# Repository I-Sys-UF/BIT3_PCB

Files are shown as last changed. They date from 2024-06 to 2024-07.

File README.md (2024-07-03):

# BIT3_PCB

KiCad 7.0.x にて設計

# BIT とは

**B**eginning **I**.Sys **T**racer のイニシャルで、新入生教育用のライントレーサの筐体です  
先代の BIT2 の設計を踏襲しつつ、マイコンを RP2040 搭載の秋月製 AE-RP2040 に置き換えました。ギアボックス等は流用できるようにしています

# 部品表

## 主要部品

| 部品番号 | 部品名 | 秋月 |
|:----|:----|:----|
| R1 - R5, R11 | 100 Ω | [125101](https://akizukidenshi.com/catalog/g/g125101/) |
| R6 - R10 | 4.7k Ω | [125273](https://akizukidenshi.com/catalog/g/g125273/) |
| R12 - R16 | 510 Ω | [125511](https://akizukidenshi.com/catalog/g/g125511/) |
| R17 - R21 | 1k Ω | [125102](https://akizukidenshi.com/catalog/g/g125102/) |
| C1 - C3 | 0.1 uF | [110147](https://akizukidenshi.com/catalog/g/g110147/) |
| D1 - D5 | 5mm LED | [113172](https://akizukidenshi.com/catalog/g/g113172/) |
| D6 | 1N4148 | [100941](https://akizukidenshi.com/catalog/g/g100941/) |
| U1 | AE-RP2040 | [117542](https://akizukidenshi.com/catalog/g/g117542/) |
| U2 - U6 | LBR-127HLD | [104500](https://akizukidenshi.com/catalog/g/g104500/) |
| U7 | MCP3008 | [109485](https://akizukidenshi.com/catalog/g/g109485/) |
| U7 | IC ソケット | [100007](https://akizukidenshi.com/catalog/g/g100007/) |
| U8 | AE-DRV8835 | [109848](https://akizukidenshi.com/catalog/g/g109848/) |
| U9 | NJM7805FA | [108678](https://akizukidenshi.com/catalog/g/g108678/) |
| Q1 | MOSFET | [107597](https://akizukidenshi.com/catalog/g/g107597/) |
| F1 | リセッタブルヒューズ | [112628](https://akizukidenshi.com/catalog/g/g112628/) |
| SW1 | 電源スイッチ | [100300](https://akizukidenshi.com/catalog/g/g100300/) |
| EXEC, MODE | タクタイルスイッチ | [103647](https://akizukidenshi.com/catalog/g/g103647/) |
| J1 | 2 列ピンヘッダ | [100080](https://akizukidenshi.com/catalog/g/g100080/) |
| J2 | バッテリ接続用ケーブル・コネクタ | 省略 |
| J3, U1 | 1 列ピンソケット | [105779](https://akizukidenshi.com/catalog/g/g105779/) |
| J5, J6 | 7 セグメント LED  | [110344](https://akizukidenshi.com/catalog/g/g110344/) |

## その他の部品

| 部品名 | 商品名 | リンク |
|:----|:----|:----|
| 前輪 | タミヤ　ボールキャスター | <https://tamiyashop.jp/shop/g/g70144> |
| 動力 | タミヤ　ダブルギヤボックス（左右独立4速タイプ） | <https://tamiyashop.jp/shop/g/g70168> |
| 後輪 | タミヤ　スリムタイヤセット | <https://tamiyashop.jp/shop/g/g70193> |
| XBee | XBee S2C ワイヤアンテナ型 | <https://www.switch-science.com/products/4089> |
| XBee 用変換基板 | XBeeエクスプローラ5Vマイコン用 | <https://www.switch-science.com/products/1166> |
| XBee 用 USB アダプタ | XBeeエクスプローラUSBドングル | <https://www.switch-science.com/products/1790> |

# 回路図

BIT3＿Schematic

# 基板デザイン

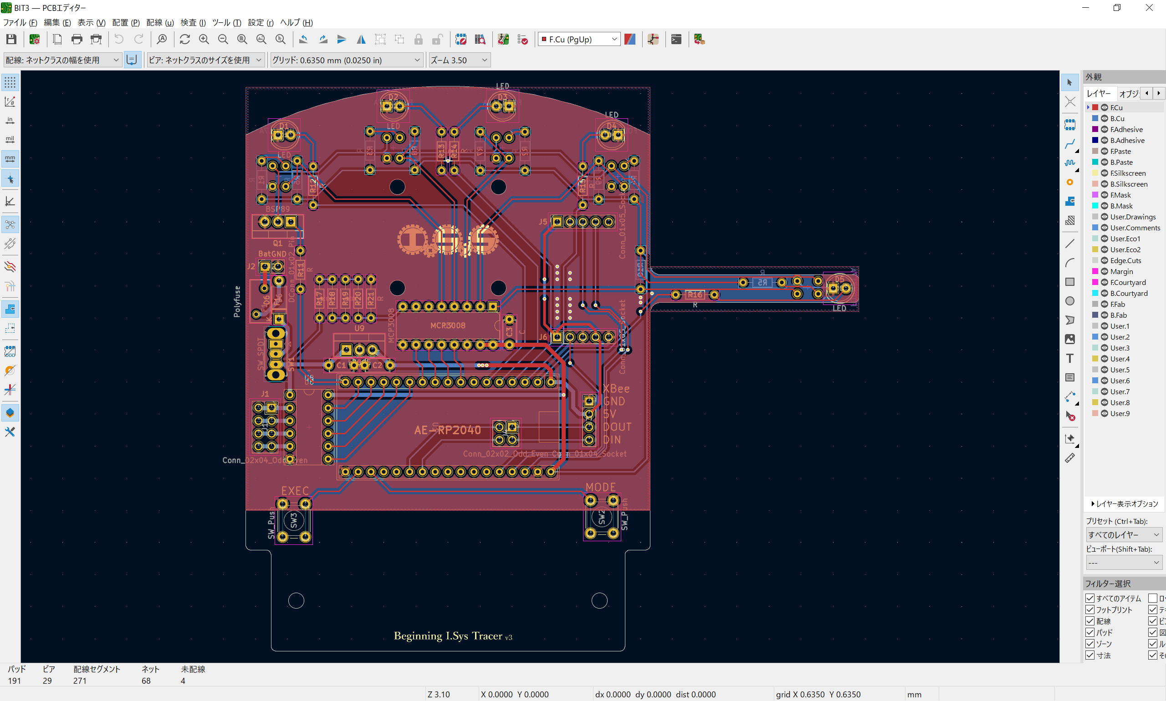
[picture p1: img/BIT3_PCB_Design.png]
BIT3＿PCB


# 更新履歴

- `v1.0`
  - 初回リリース
- `v1.1`
  - ADC にバッテリ電圧が直接入力される問題を修正
- `v1.2`
  - 接続されていない GND ベタが存在する問題を修正
- `v1.3`
  - モータ・ドライバに電源が供給されていない問題を修正
- `v1.4`
  - ADC IC MCP3008 にパスコンを追加
- `v1.5` 
  - 前輪と部品が微妙に干渉する問題を修正
- `v1.6`
  - 逆接防止ダイオードの追加、バッテリ入力の接続の変更、一部部品の変更（基板には影響なし）
- `v1.7`
  - フォトセンサを変更
- `v2.0`
  - XBee 接続用のコネクタを追加
- `v2.1`
  - BACK を EXEC に変更
- `v2.2`
  -  フォトセンサ駆動用トランジスタを変更
- `V2.3`
  - 7 セグメント LED モジュール用フットプリントを追加
  - センサ位置を微調整

# ライセンス

<br />この 作品 は <a rel="license" href="http://creativecommons.org/licenses/by-nc-nd/4.0/">クリエイティブ・コモンズ 表示 - 非営利 - 改変禁止 4.0 国際 ライセンス</a>の下に提供されています。

利用を希望される方は部の[公式 Twitter ](https://twitter.com/ISys_robocon)までご連絡ください

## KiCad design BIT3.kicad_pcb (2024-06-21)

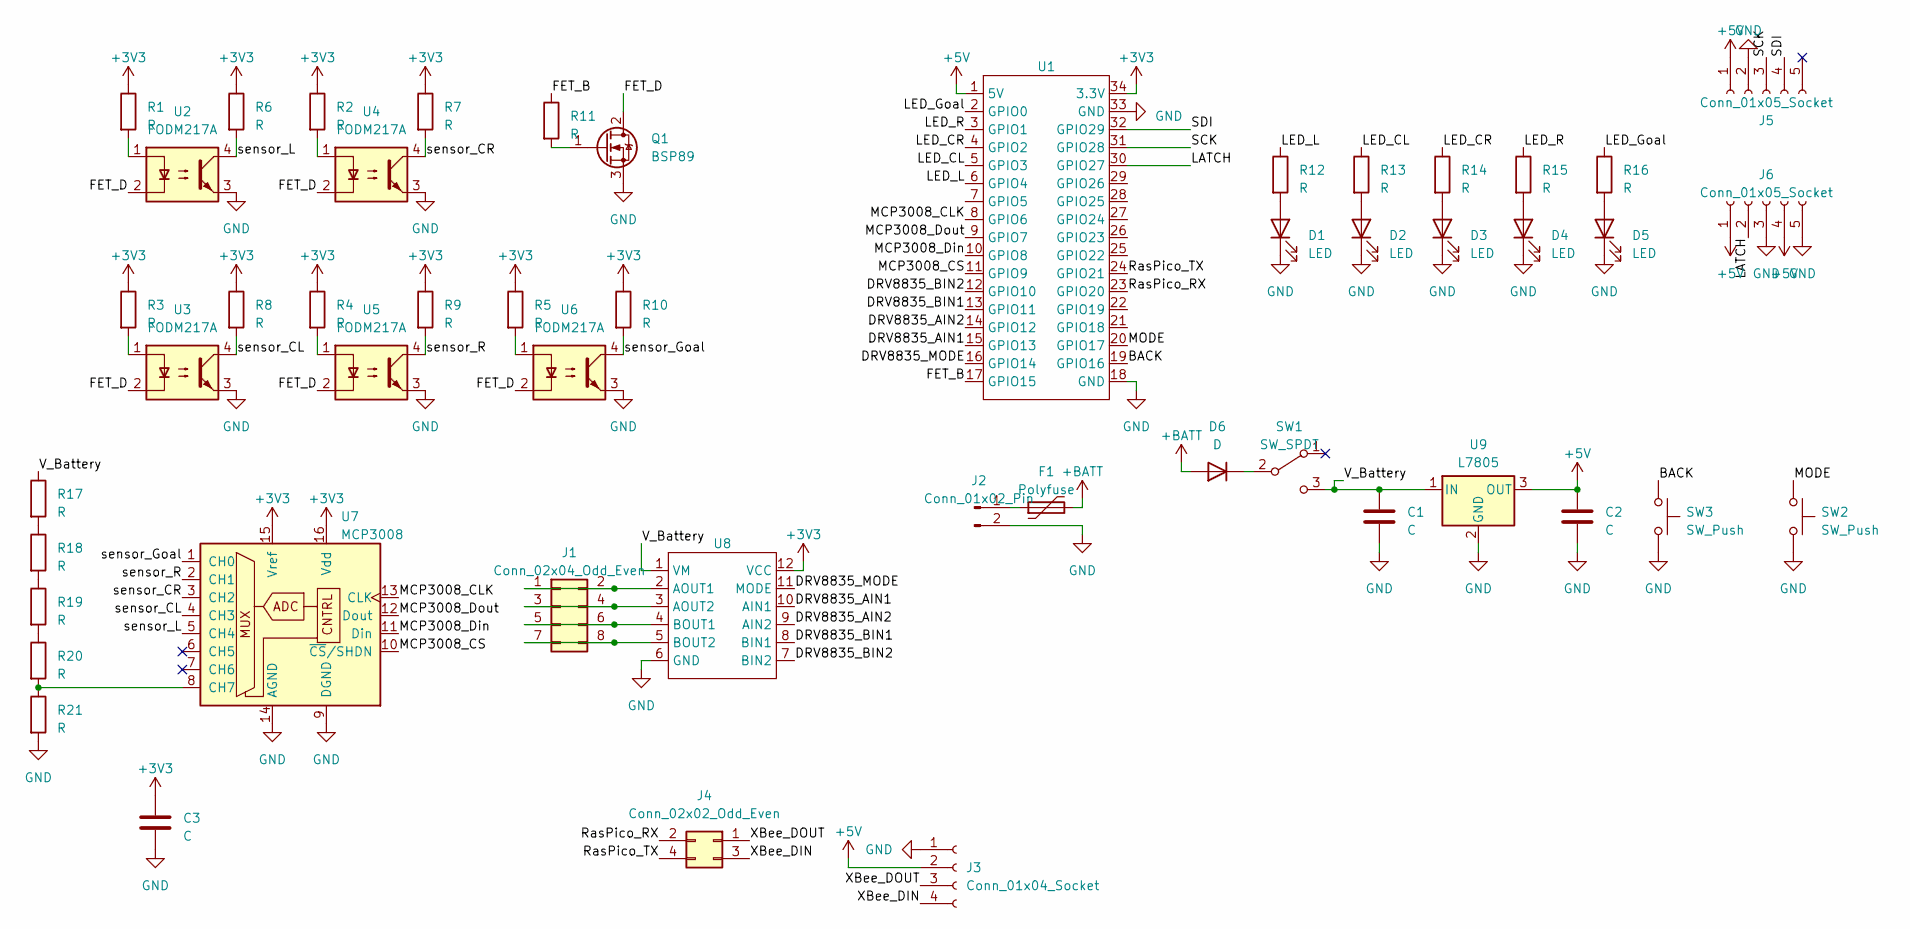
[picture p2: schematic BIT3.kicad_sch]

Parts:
C1, C2, C3: C; C_Disc_D4.7mm_W2.5mm_P5.00mm
D1, D2, D3, D4, D5: LED; LED_D5.0mm
D6: D; D_A-405_P7.62mm_Horizontal
F1: Polyfuse; Fuse_BelFuse_0ZRE0005FF_L8.3mm_W3.8mm
J1: Conn_02x04_Odd_Even; PinSocket_2x04_P2.54mm_Vertical
J2: Conn_01x02_Pin; PinSocket_1x02_P2.54mm_Vertical
J3: Conn_01x04_Socket; PinSocket_1x04_P2.54mm_Vertical
J4: Conn_02x02_Odd_Even; PinSocket_2x02_P2.54mm_Vertical
J5, J6: Conn_01x05_Socket; PinSocket_1x05_P2.54mm_Vertical
Q1: BSP89; TO-220-3_Vertical
R1, R2, R3, R4, R5, R6, R7, R8, R9, R10, R11, R12, R13, R14, R15, R16, R17, R18, R19, R20, R21: R; R_Axial_DIN0204_L3.6mm_D1.6mm_P7.62mm_Horizontal
SW1: SW_SPDT; SW_Slide_1P2T_CK_OS102011MS2Q
SW2, SW3: SW_Push; SW_PUSH_6mm
U1: AE-RP2040
U2, U3, U4, U5, U6: FODM217A; LBR-127HLD
U7: MCP3008; DIP-16_W7.62mm
U8: AE-DRV8835
U9: L7805; TO-220-3_Vertical

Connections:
+3V3: C3.1, R1.1, R2.1, R3.1, R4.1, R5.1, R6.1, R7.1, R8.1, R9.1, R10.1, U1.34 (3.3V), U7.15 (Vref), U7.16 (Vdd), U8.12 (VCC)
+5V: C2.1, J3.2, J5.1, J6.1, J6.4, U1.1 (5V), U9.3 (OUT)
+BATT: D6.2 (A), F1.2
/BACK: SW3.1, U1.19 (GPIO16)
/DRV8835_AIN1: U1.15 (GPIO13), U8.10 (AIN1)
/DRV8835_AIN2: U1.14 (GPIO12), U8.9 (AIN2)
/DRV8835_BIN1: U1.13 (GPIO11), U8.8 (BIN1)
/DRV8835_BIN2: U1.12 (GPIO10), U8.7 (BIN2)
/DRV8835_MODE: U1.16 (GPIO14), U8.11 (MODE)
/FET_B: R11.1, U1.17 (GPIO15)
/FET_D: Q1.2 (D), U2.2, U3.2, U4.2, U5.2, U6.2
/LATCH: J6.2, U1.30 (GPIO27)
/LED_CL: R13.1, U1.5 (GPIO3)
/LED_CR: R14.1, U1.4 (GPIO2)
/LED_Goal: R16.1, U1.2 (GPIO0)
/LED_L: R12.1, U1.6 (GPIO4)
/LED_R: R15.1, U1.3 (GPIO1)
/MCP3008_CLK: U1.8 (GPIO6), U7.13 (CLK)
/MCP3008_CS: U1.11 (GPIO9), U7.10 (~CS/SHDN)
/MCP3008_Din: U1.10 (GPIO8), U7.11 (Din)
/MCP3008_Dout: U1.9 (GPIO7), U7.12 (Dout)
/MODE: SW2.1, U1.20 (GPIO17)
/RasPico_RX: J4.2, U1.23 (GPIO20)
/RasPico_TX: J4.4, U1.24 (GPIO21)
/SCK: J5.3, U1.31 (GPIO28)
/SDI: J5.4, U1.32 (GPIO29)
/V_Battery: C1.1, R17.1, SW1.3 (C), U8.1 (VM), U9.1 (IN)
/XBee_DIN: J3.4, J4.3
/XBee_DOUT: J3.3, J4.1
/sensor_CL: R8.2, U3.4, U7.4 (CH3)
/sensor_CR: R7.2, U4.4, U7.3 (CH2)
/sensor_Goal: R10.2, U6.4, U7.1 (CH0)
/sensor_L: R6.2, U2.4, U7.5 (CH4)
/sensor_R: R9.2, U5.4, U7.2 (CH1)
GND: C1.2, C2.2, C3.2, D1.1 (K), D2.1 (K), D3.1 (K), D4.1 (K), D5.1 (K), J2.2, J3.1, J5.2, J6.3, J6.5, Q1.3 (S), R21.2, SW2.2, SW3.2, U1.18 (GND), U1.33 (GND), U2.3, U3.3, U4.3, U5.3, U6.3, U7.9 (DGND), U7.14 (AGND), U8.6 (GND), U9.2 (GND)
unnamed: D1.2 (A), R12.2
unnamed: D2.2 (A), R13.2
unnamed: D3.2 (A), R14.2
unnamed: D4.2 (A), R15.2
unnamed: D5.2 (A), R16.2
unnamed: D6.1 (K), SW1.2 (B)
unnamed: J1.1, J1.2, U8.2 (AOUT1)
unnamed: J1.3, J1.4, U8.3 (AOUT2)
unnamed: J1.5, J1.6, U8.4 (BOUT1)
unnamed: J1.7, J1.8, U8.5 (BOUT2)
unnamed: F1.1, J2.1
unnamed: Q1.1 (G), R11.2
unnamed: R1.2, U2.1
unnamed: R2.2, U4.1
unnamed: R3.2, U3.1
unnamed: R4.2, U5.1
unnamed: R5.2, U6.1
unnamed: R17.2, R18.1
unnamed: R18.2, R19.1
unnamed: R19.2, R20.1
unnamed: R20.2, R21.1, U7.8 (CH7)

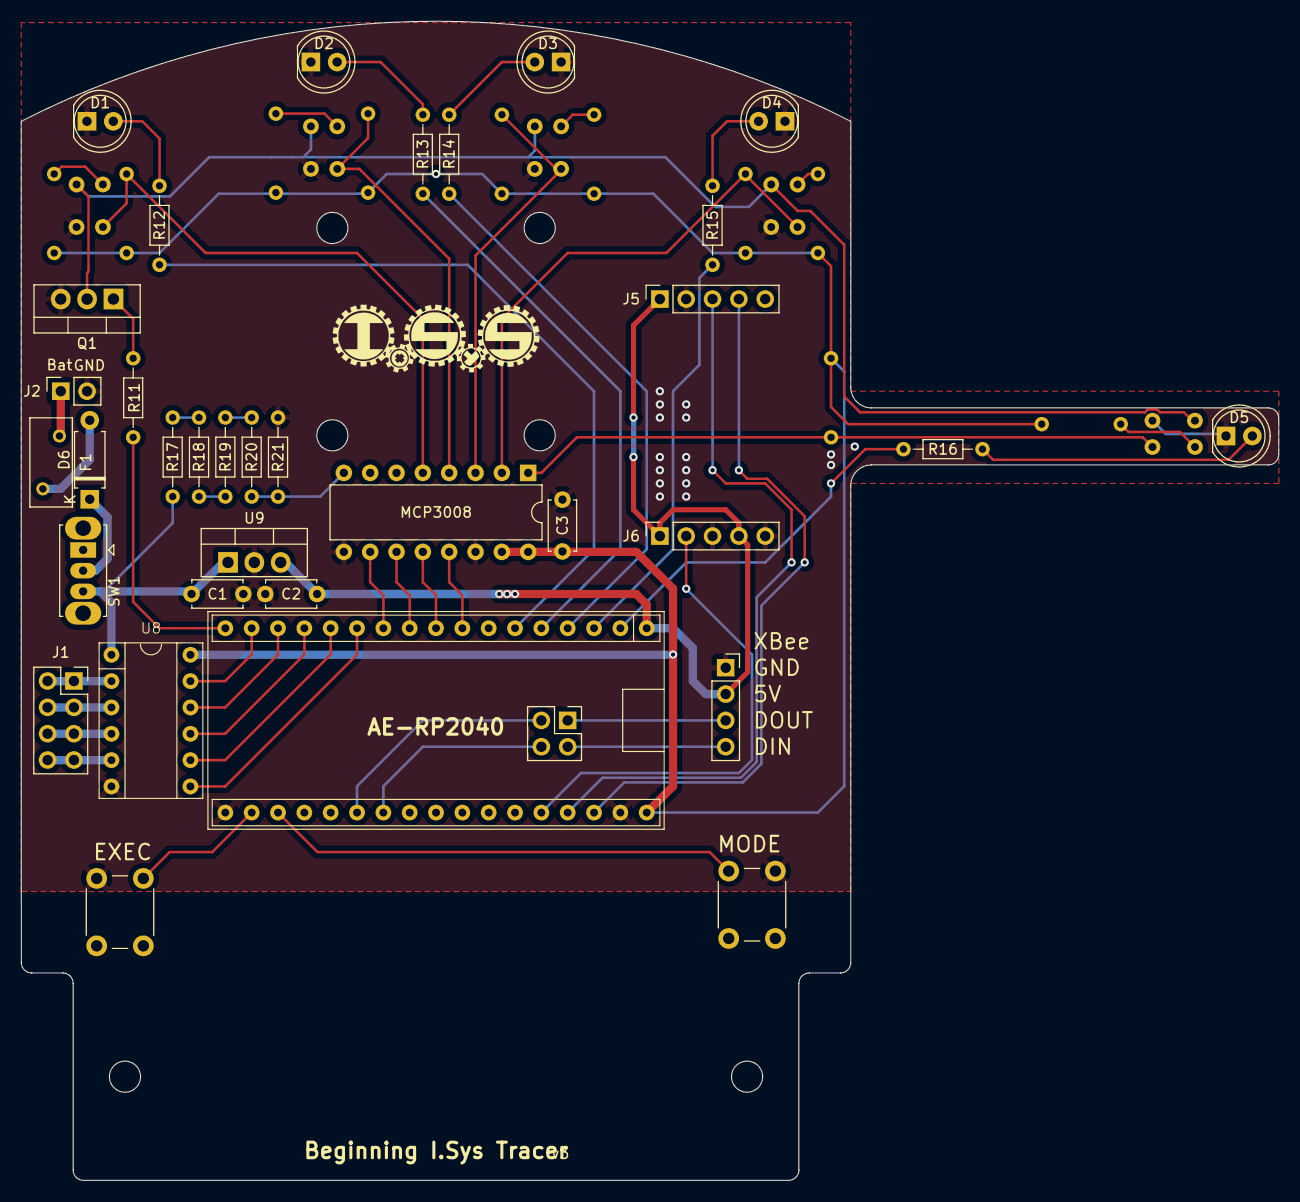
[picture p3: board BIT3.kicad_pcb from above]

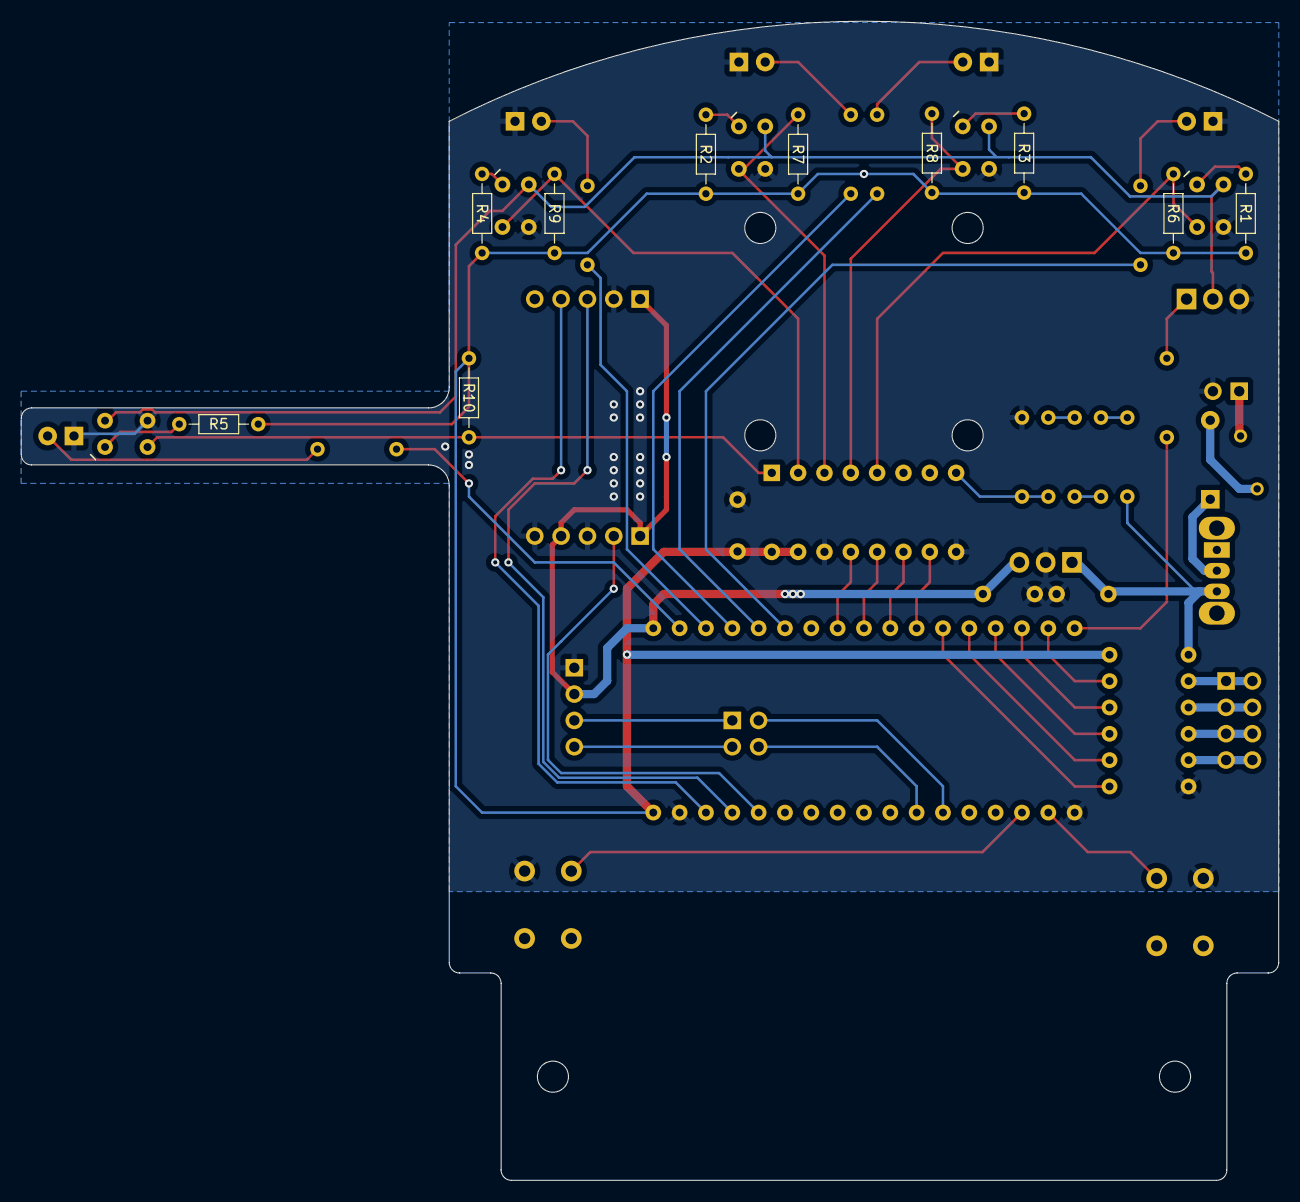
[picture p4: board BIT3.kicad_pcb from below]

Board: 2 copper layers, 121.3 x 111.8 mm, 50 parts (15 on the bottom side), 56 nets.

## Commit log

2023-06-04 Update PCB Design
    [BIT3.kicad_pcb]
2023-06-04 部品表を追加
2023-06-04 Update PCB Design
    - remove `SW2` and `SW3` silkscreen
    - add silkscreen print
    - `SW2` as `MODE`, `SW3` as `BACK`
    [BIT3.kicad_pcb]
2023-06-05 Update PCB Design
    add GND vias
    [BIT3.kicad_pcb]
2023-06-05 更新履歴を追加
2023-06-05 Update PCB Design
    fix Power Supply
    [BIT3.kicad_pcb]
2023-06-09 add PCB Design
2023-06-09 画像ファイルパス変更に合わせ画像リンクを更新
2023-06-09 基板更新
    MCP3008 にパスコンを追加
    [BIT3.kicad_pcb, BIT3.kicad_sch]
2023-06-29 逆説防止 D を追加, バッテリ電圧監視 ADC の配置を変更
    [BIT3.kicad_pcb, BIT3.kicad_sch]
2023-06-29 部品表更新
2023-06-29 フォトセンサを変更
    [BIT3.kicad_pcb, BIT3.kicad_sch]
2023-06-30 XBee を接続できるように変更
    [BIT3.kicad_pcb, BIT3.kicad_sch]
2023-06-30 更新履歴を追記
2023-07-02 モータの電源を BATT から 5V に変更
    [BIT3.kicad_pcb, BIT3.kicad_sch]
2023-07-04 モータ電源を BATT に戻した
    [BIT3.kicad_pcb, BIT3.kicad_sch]
2023-07-04 画像更新
2023-07-18 BACK -> EXEC
    [BIT3.kicad_pcb]
2023-07-18 部品表追記
2023-08-02 フォトリフレクタを変更
2023-11-09 R1 - R5 の抵抗値を変更
2024-02-05 赤外線 LED 用トランジスタを変更
    [BIT3.kicad_pcb, BIT3.kicad_sch]
2024-04-10 Tr 置き換え，部品表更新
    [BIT3.kicad_pcb, BIT3.kicad_sch]
2024-04-27 7 セグメント LED 用フットプリントを追加
    [BIT3.kicad_pcb, BIT3.kicad_sch]
2024-06-11 センサ位置修正
    [BIT3.kicad_pcb]
2024-06-11 部品変更
2024-06-21 センサ位置調整
    [BIT3.kicad_pcb]
2024-06-21 更新履歴追記

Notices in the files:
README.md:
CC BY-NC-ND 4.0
